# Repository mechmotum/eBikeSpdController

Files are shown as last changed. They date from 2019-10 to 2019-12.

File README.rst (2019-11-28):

eBikeSpdController
==================

This repo contains the source files for the design, implementation and testing of a cruise control system for an instrumented electric bicycle. Additionally, this repo contains project documentation in the form of a user/technical guide and master electrical schematic for the cruise control system. Newcomers to this project should begin by reading the user/technical guide.  

Controller Design Source Code
-----------------------------
The design folder contains MATLAB code that can be used to replicate the results of the controller design process outlined in this blog post here: https://mechmotum.github.io/blog/ebike-controller-design.html 

To replicate the controller design process, download the .m files in the design folder and run them in 
the following order: SystemID.m -> ControllerTuning.m -> ControllerRobustnessTesting.m -> ControllerEval.m. 
For more information, see the blog post mentioned above.

Implementation Source Code 
--------------------------
The Implementation folder contains the .ino file used to implement the derived contoller on an Arduino nano augmented to the powertrain of an electric bicycle. Please see this blog post for more information on how this software fits into the overall system: 
https://mechmotum.github.io/blog/ebike-controller-implementation.html

Testing Source Code 
-------------------
The Testing folder contains the source code used in the evaluation and diagnostics of the cruise control system implementation. The boxplot figure codes contain the code used to create the boxplot figures shown in the paper and poster presented at the 2019 Bicycle and Motorcycle Dynamics Conference. These materials can be found here: https://mechmotum.github.io/blog/ebike-controller-bmd-presentation.html 

Also included in the Testing folder is a utility function for converting bits to volts and the testAnalyzer.m file used to plot and evaluate the performance of runs collected from testing. 

Please see each file for more information on what's included in them. These files are meant to be used with the comma delimited diagnostics files produced by the TopLevel.ino file found in the Implementation folder of this repo. 

Other Documents in this Repo
---------------------------- 
Also included in this repository are the user+technical guide for the cruise control system (pdf) and a copy of the master electrical schematic for the cruise control system (pdf). Note: The master electrical schematic is also included as a .json file for opening and editing in easyEDA.

Prerequisites
-------------

Software

You will need MATLAB R2018b or above with the Control System and Robust Control Toolboxes installed. Also needed is the Arduino IDE with the 
PID_v1 and PinChangeInterrupt libraries. 

Hardware 

Hardware prerequisites can be found on the implementation blog post mentioned above.

Authors
-------

Trevor Metz 
UC Davis Mechanical Engineering 2019
tzmetz@ucdavis.edu

Acknowledgments
---------------
Jason K. Moore for support and guidance 

Nicholas Chan for help with the Arduino code 

Brett Beauregard for developing the PID Arduino Library heavily used in the Implementation code 

Grey Gnome for developing the pin change interrupt library used in the Implementation code

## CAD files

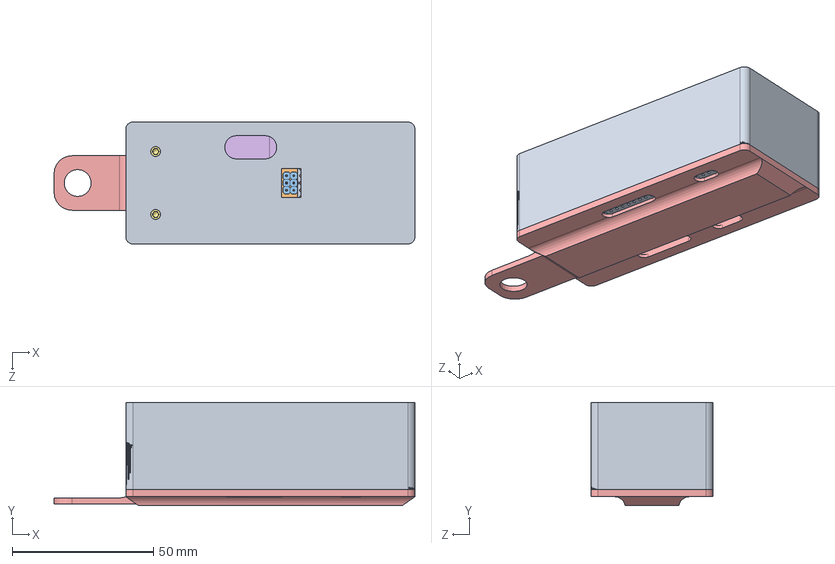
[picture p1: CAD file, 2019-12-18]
CADfiles/Nano Housing/Arduino Housing Master Assembly.SLDASM
127.8 x 36.5 x 43.2 mm
Arduino Nano V3 PCB.ipt
Housing male header - single.ipt x 36
Pin male header straight - single.ipt x 36
Base_ArduinoHousing
socket head cap screw_am x 2
HeatSetInsert x 2
FlatTopNanoHousingCover

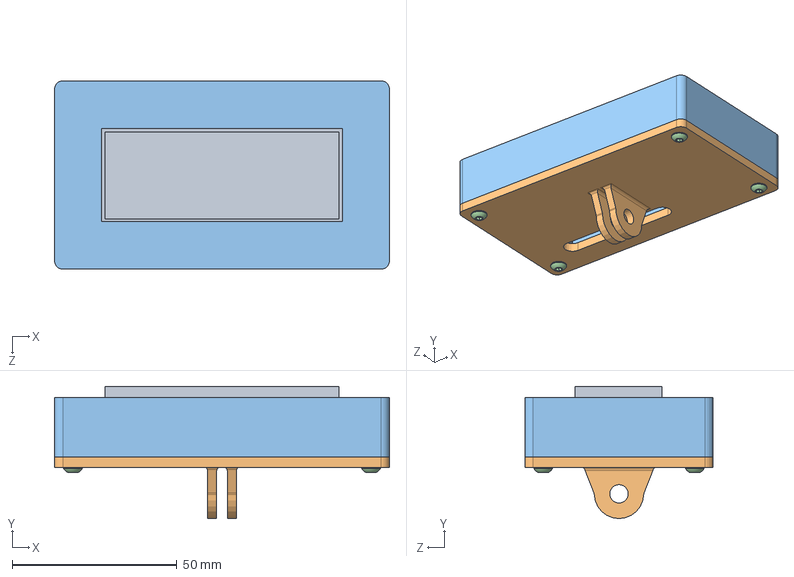
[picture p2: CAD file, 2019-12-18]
CADfiles/LCD Housing/LCDHousing_Assem_G2.SLDASM
101.6 x 40.1 x 57.1 mm
LCD_G2
LCDHousing_Bot_G2
LCDHousing_Top_G2
socket button head cap screw_am x 4
HeatSetInsert x 4

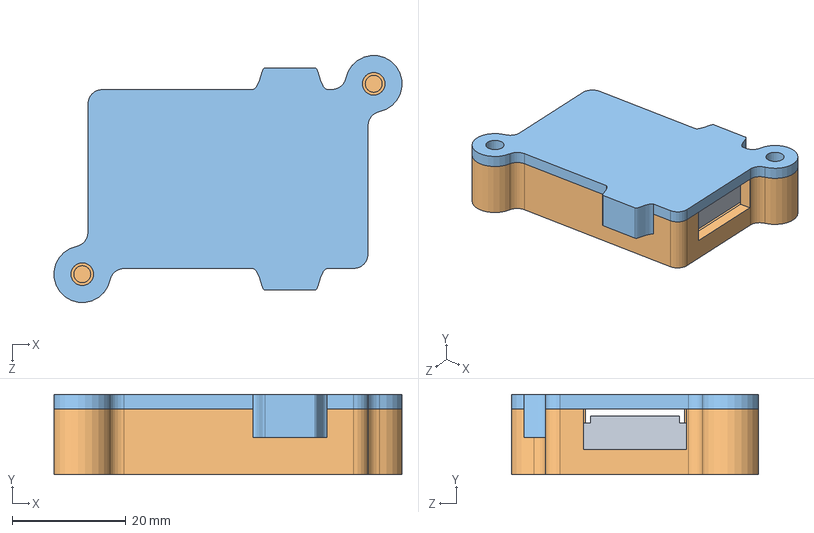
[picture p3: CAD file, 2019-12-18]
CADfiles/MicroSDCardHousing/M_SDCardHousing_MasterAssem.SLDASM
61.3 x 14.1 x 43.5 mm
microSDCardModule
Base_MicroSDCardModule
cover_MSDHousing

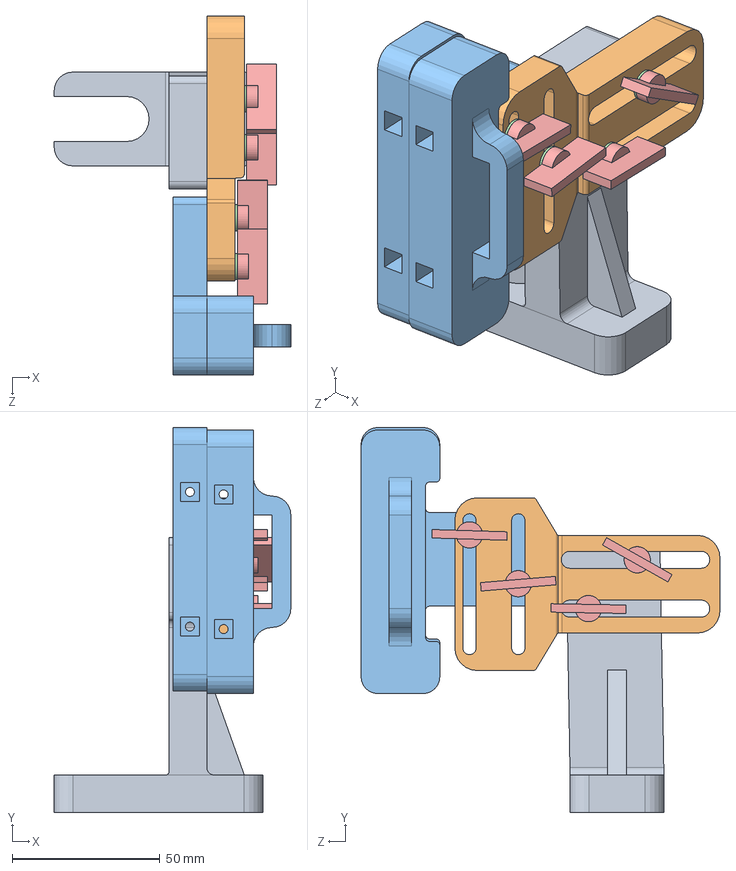
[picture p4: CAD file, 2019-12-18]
CADfiles/SafetySwitch/ReedSwitch/ReedSwitchAssemV2.SLDASM
80.1 x 130.3 x 121.4 mm
StayClamp_Top
AdjusterArm
SwitchMountBot x 2
M4Washer x 8
WingNut x 4

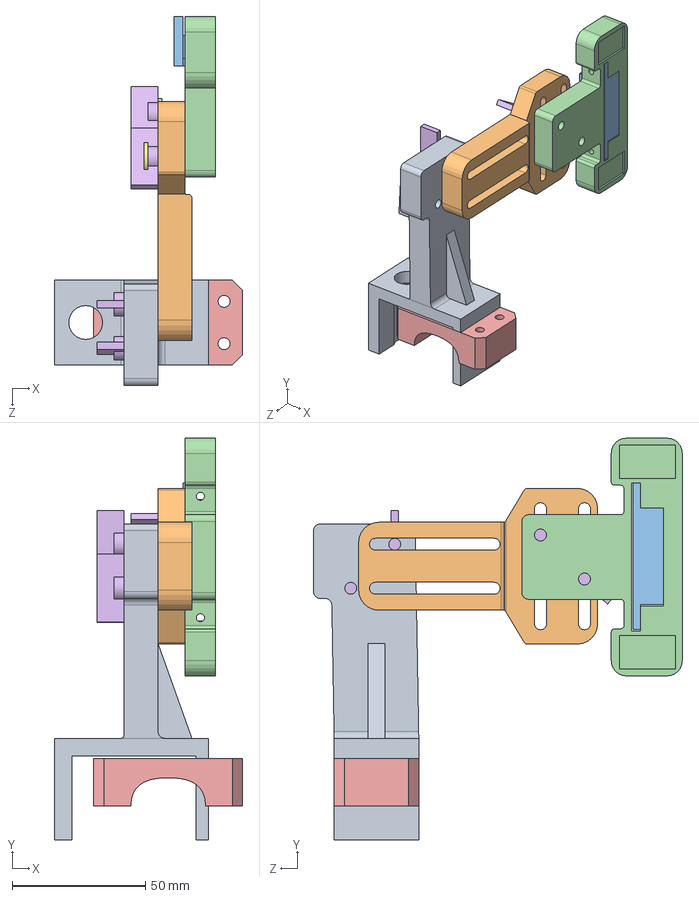
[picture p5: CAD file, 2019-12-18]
CADfiles/SafetySwitch/ReedSwitch/ReedSwitchAssem.SLDASM
70.7 x 150.7 x 138.4 mm
StayClamp_Top
AdjusterArm
ReedSwitchBlank
SwitchMountBot
StayClamp_Bot
WingNut x 4
flat washer regular_am x 4

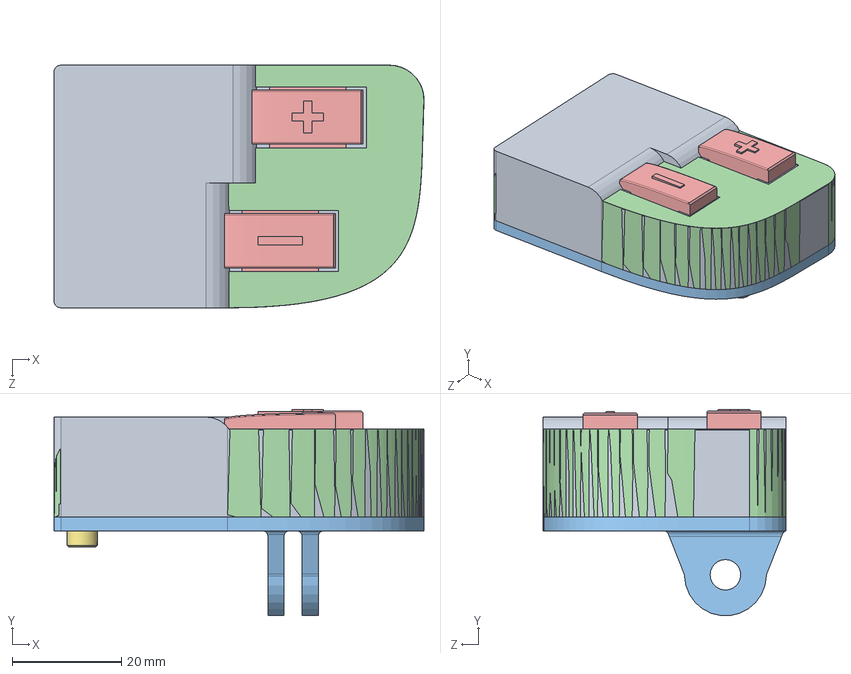
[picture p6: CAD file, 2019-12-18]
CADfiles/Button Housing/MasterAssembly.SLDASM
67.7 x 37.7 x 44.5 mm
PerfBoard
PushButton x 2
ButHousing_Base
ButtHousingCoverV2

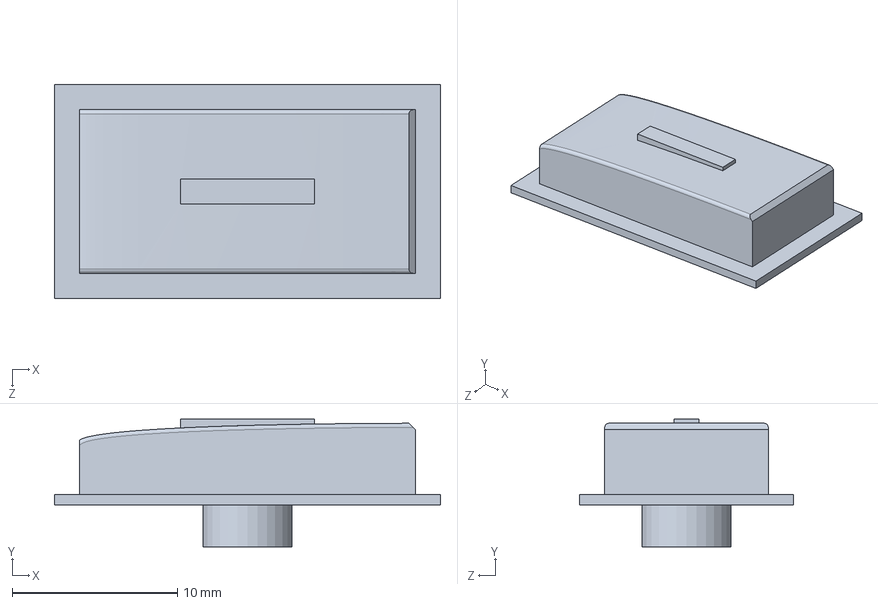
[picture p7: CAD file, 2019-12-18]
CADfiles/Button Housing/Button.SLDPRT
23.4 x 7.75 x 13.0 mm

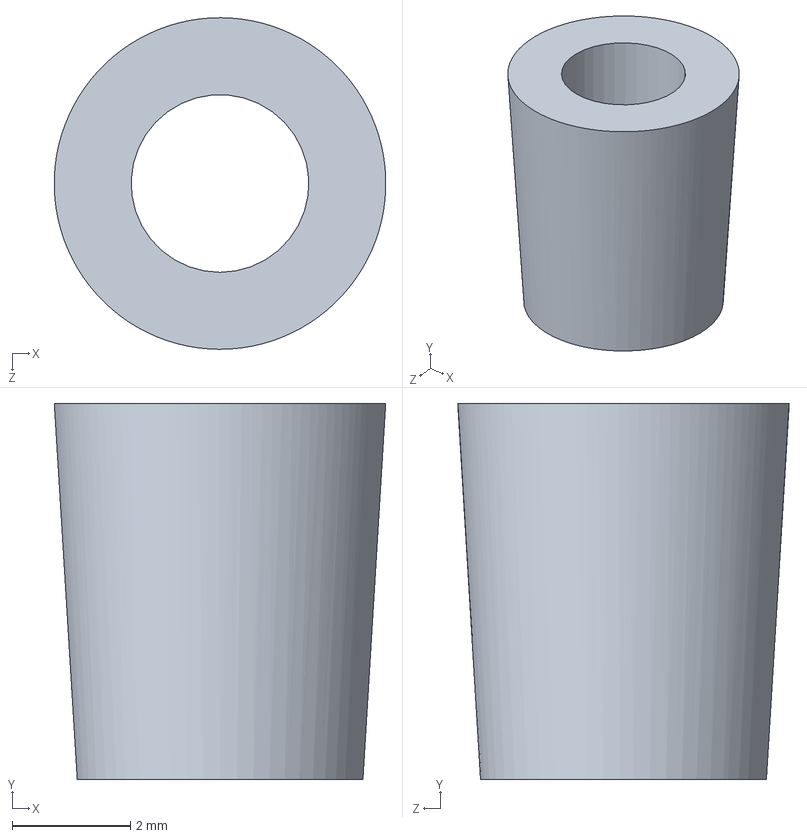
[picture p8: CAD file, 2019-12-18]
CADfiles/HeatSetInsert.SLDPRT
5.60 x 6.35 x 5.60 mm

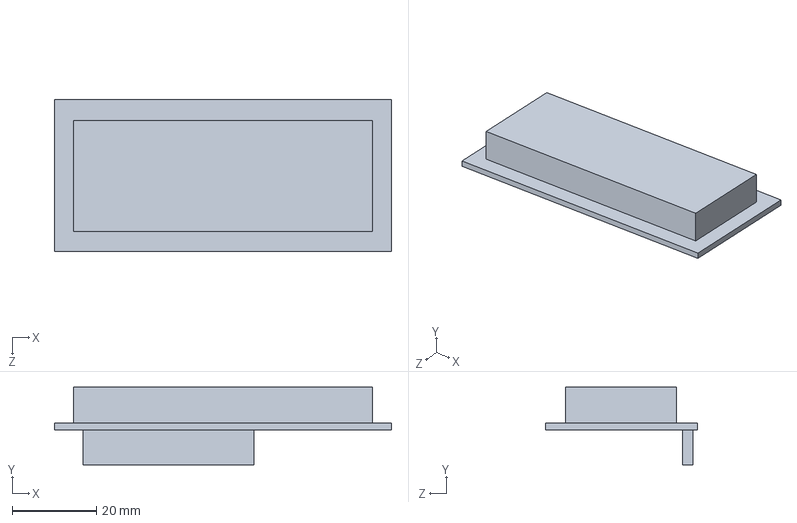
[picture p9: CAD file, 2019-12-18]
CADfiles/LCD Housing/LCD_G2.SLDPRT
79.9 x 18.5 x 36.0 mm

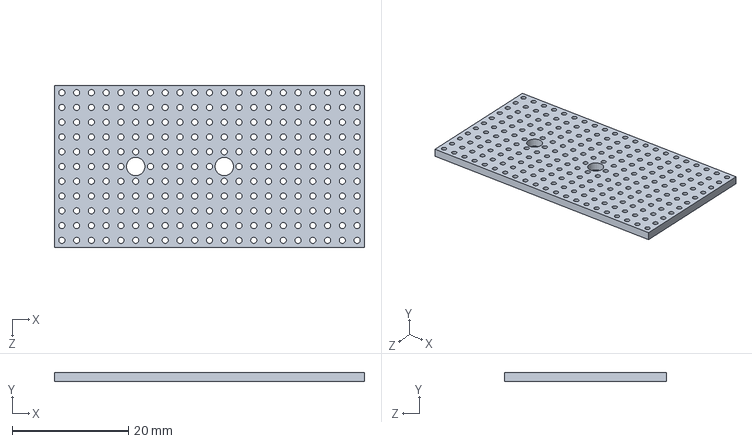
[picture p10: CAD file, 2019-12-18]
CADfiles/Nano Housing/StripBoard.SLDPRT
53.3 x 1.59 x 27.9 mm

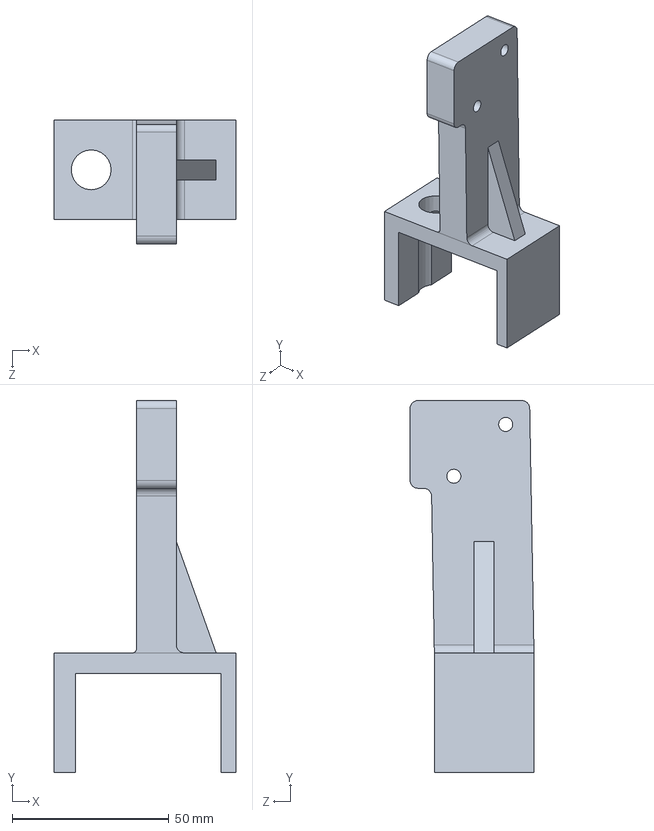
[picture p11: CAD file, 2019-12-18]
CADfiles/SafetySwitch/ReedSwitch/StayClamp_Top.SLDPRT
57.9 x 118.5 x 39.5 mm

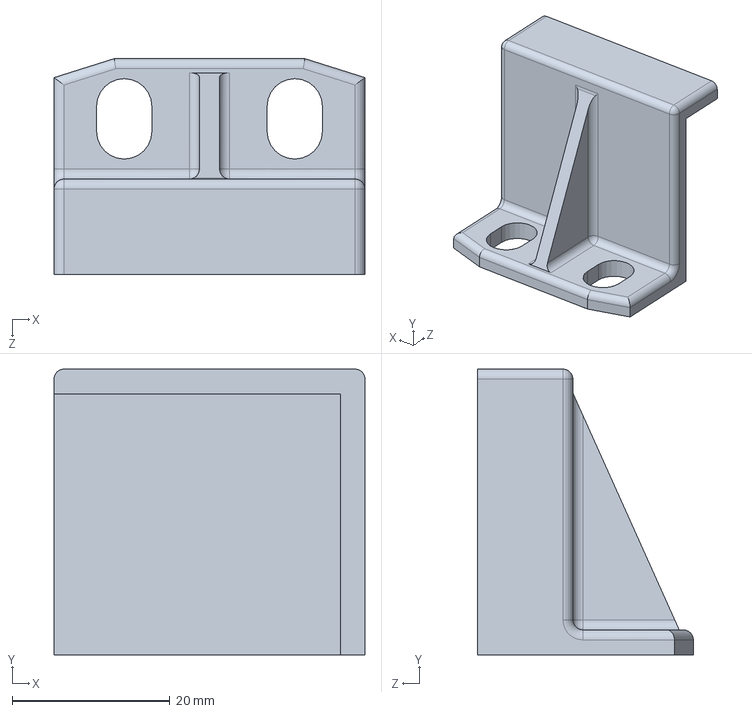
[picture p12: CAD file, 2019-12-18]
CADfiles/SafetySwitch/Relay Clamp Top.SLDPRT
39.4 x 36.2 x 27.3 mm

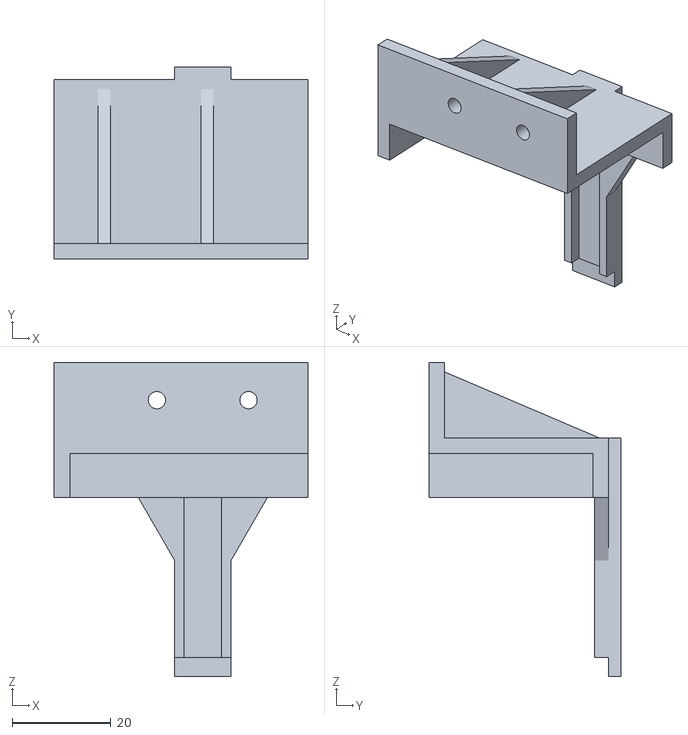
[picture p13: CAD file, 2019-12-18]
CADfiles/SafetySwitch/STL/Relay Clamp Bot_NOFILLET.STL
51.3 x 38.9 x 63.5

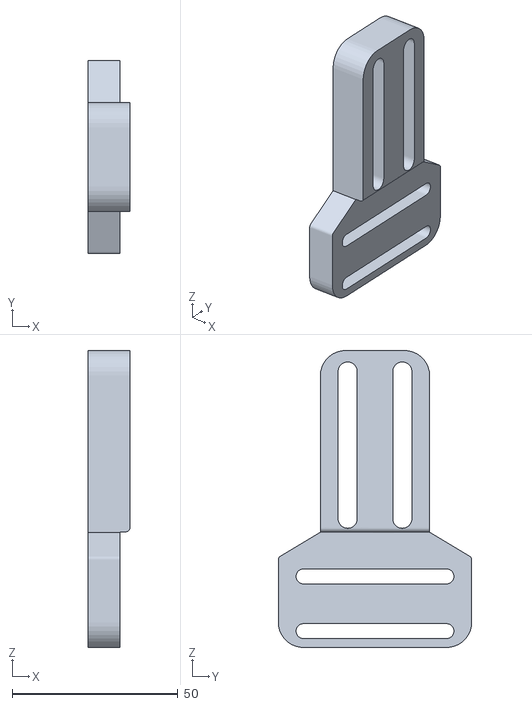
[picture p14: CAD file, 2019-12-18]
CADfiles/SafetySwitch/STL/V2 Reed Switch/AdjusterArm.STL
12.7 x 58.4 x 89.7

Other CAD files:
CADfiles/Nano Housing/Arduino Nano V3 assemble.SLDASM
CADfiles/MicroSDCardHousing/Base_MicroSDCardModule.sldprt
CADfiles/Button Housing/ButtHousingCoverV2.sldprt
CADfiles/LCD Housing/LCDHousing_Top_G2.sldprt
CADfiles/Button Housing/ButHousing_Base.sldprt
CADfiles/Button Housing/ButHousing_Top.sldprt
CADfiles/Button Housing/PerfBoard.SLDPRT
CADfiles/Button Housing/PushButton.SLDPRT
CADfiles/Button Housing/Spring.SLDPRT
CADfiles/LCD Housing/LCDHousing_Bot_G2.SLDPRT
CADfiles/MicroSDCardHousing/cover_MSDHousing.sldprt
CADfiles/MicroSDCardHousing/microSDCardModule.SLDPRT
CADfiles/Nano Housing/Base_ArduinoHousing.sldprt
CADfiles/Nano Housing/Cover_ArduinoHousing.sldprt
CADfiles/Nano Housing/FlatTopNanoHousingCover.sldprt
CADfiles/Nano Housing/arduino-nano-v3/Arduino Nano V3 PCB.ipt
CADfiles/Nano Housing/arduino-nano-v3/Arduino Nano V3 assemble.iam
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

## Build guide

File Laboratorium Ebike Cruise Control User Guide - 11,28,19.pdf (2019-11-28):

## Laboratorium Electric Bicycle Cruise Control System Operating and Technical Guide

Introduction
This guide is here to help you understand both how to use the cruise control system and how to understand the technical details behind the design and implementation of the cruise control system.

Cruise Control System User’s Guide
The cruise control system maintains the electric bicycle’s speed at a user set desired speed in m/s. This action is performed through automatic modulation of the throttle via an Arduino nano programmed with a simple PID controller. The Arduino Nano sits inline with the throttle output signal. When the cruise control is engaged, the Ardino works by emulating the rider’s throttle inputs to maintain the speed of the electric bicycle at the user set desired speed.

The cruise control system can be engaged when riding the bike. The following outlines the steps the user needs to take to engage and operate the cruise control:

1. To power all systems the following needs to be performed:
a. Before beginning, make sure that the dead man’s ankle velcro switch is attached to its mount near the foot peg
b. First power the Arduino nano and dead man’s switch by flipping the switch to the NiCd battery pack. The onboard Arduino LEDs will flicker on.
c. Next power the electric bicycle by flipping the rocker switch on the bottom of the Li+ battery cylinder on the seat tube. To verify the battery switch is in the “on” position, press the battery level indicator button on the top of the battery. There should be an array of multicolored LEDs that light up showing the current capacity of the battery.
d. Finally, press the red switch on the side of the throttle. The LEDs on the throttle will light up indicating the bicycle is ready for riding
2. With the dead man’s ankle velcro switch still attached to the bicycle, tie the switch to the rider’s ankle. Another person may be needed to hold the bicycle upright.
3. Start riding the bicycle.
4. Accelerate or deccelerate to around the desired setpoint (target) speed.

5. Engage the cruise control by pressing the two cruise control buttons at the same time. The LCD screen will change to show the setpoint speed and the current speed.
a. Note that the setpoint speed initializes itself at the speed of the bicycle the moment the cruise control is engaged.
6. Once engaged, the Arduino Nano will take control of the throttle and the user can sit back and steer.
a. At any time, manual control of the throttle can be returned to the user by simply pressing all the way down on the throttle with your thumb (This will deactivate the cruise control).
7. While the cruise control is engaged the cruise control buttons can be pressed to either increment or decrement the setpoint speed.
8. To disengage the cruise control simply press all the way down on the throttle. A message confirming that the cruise control has disengaged will print to the LCD.
9. Steps 4-8 can be repeated any time during the ride

Reverting the Electric Bicycle to its Original Powertrain
To revert the electric bicycle back to its original powertrain, the throttle output signal (from its hall effect sensor) needs to be jumped directly to the motor controller. See below for the steps on how to do this.
1. Locate the throttle junction. This is located around the top triangle of the frame right above the head tube. See the picture below for reference:

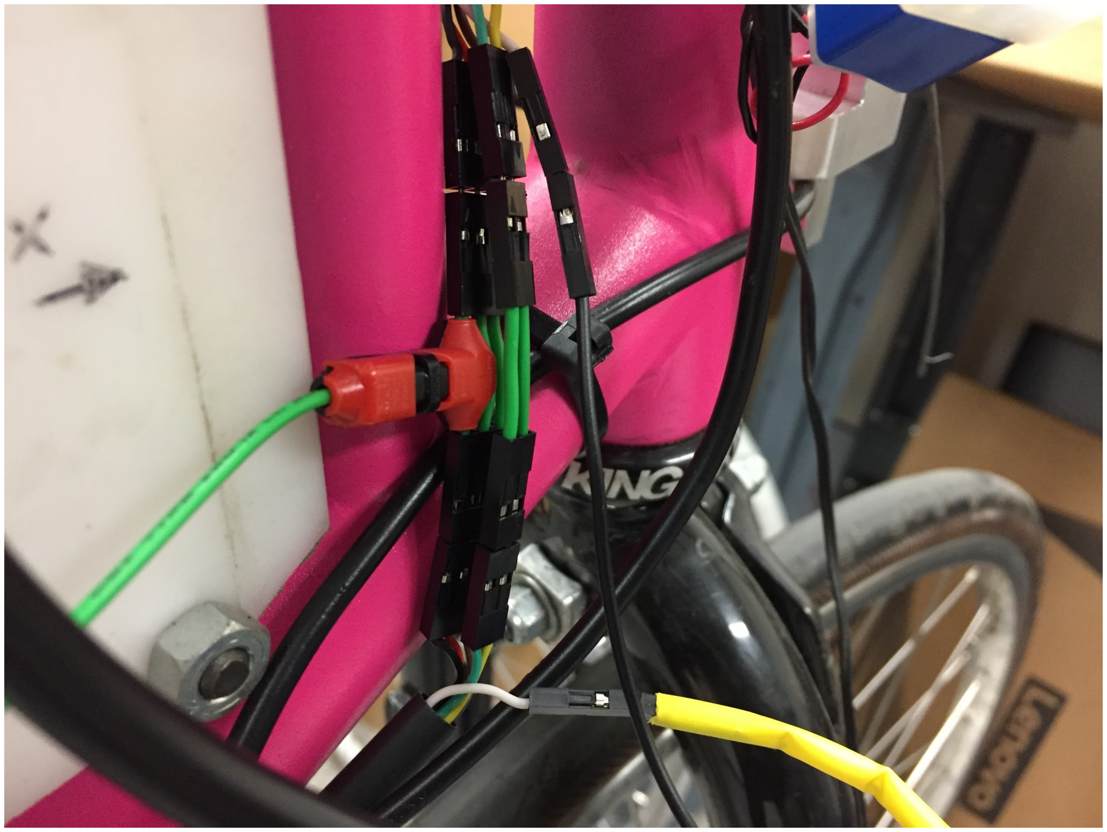
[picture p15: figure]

Note: The schematic for this junction can be found on sheet 3 of the master electrical schematic
2. Once located, disconnect the black and yellow wires. (Note the yellow wire is sleeved in a yellow sleeve).
3. To jump the throttle signal directly to the motor controller you will need to add a jumper wire to connect the white wires together. The picture below shows the jumper wire used to connect both the white wires together.

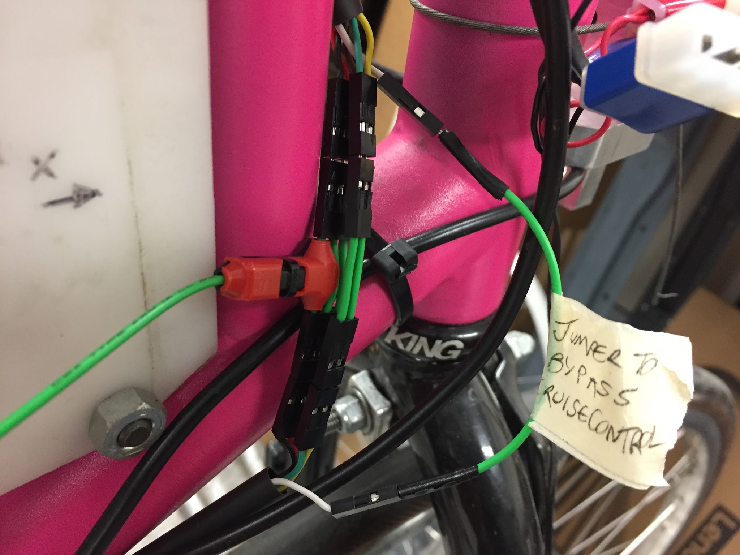
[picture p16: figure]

4. Once this is complete the Arduino should have no effect on the bike’s powertrain and it should work normally again.

Cruise Control System Technical Guide
This technical guide is meant to help you understand what went into the design and implementation of the cruise control system. There is a number of documents regarding the technical details and design of the cruise control system; these are outlined here:
1. Project Technical Poster and Paper (https://mechmotum.github.io/blog/ebike-controller-bmd-presentation.html)
a. These give a good high level overview of the project and its technical details making them a good place to start
2. Davis Instrumented Bike (https://moorepants.github.io/dissertation/davisbicycle.html) (Wheel Rate and Calibration Sections)
a. This gives a good description of the instrumented bike platform and how to go about interacting with it
3. Controller Design Blog Post (https://mechmotum.github.io/blog/ebike-controller-design.html)
a. This blog post outlines the details of the controller design process used to derive and tune the PID controller
4. Project Code Description (See eBikeSpdController Github Repository Read Me)
a. This Read Me outlines the files contained in the repository
5. Controller Design MATLAB Code (https://github.com/mechmotum/eBikeSpdController/tree/master/Design)

6. Controller Implementation Blog Post (https://mechmotum.github.io/blog/ebike-controller-implementation.html)
a. This blog post describes the physical implementation of the PID controller onto the electric bicycle
7. Arduino Code (https://github.com/mechmotum/eBikeSpdController/tree/master/Implementation/TopLevel)
8. System Electrical Schematic (https://github.com/mechmotum/eBikeSpdController)

Reading these documents in the order suggested here should give you a good enough understanding of the technical design and details of the cruise control system in order to make modifications or adjustments to the system.

Technical Troubleshooting Tips
Over the course of working on the bike, a couple common issues have arisen. These are detailed below:
1. Anderson Power Pole Contacts
a. Issue: Arduino won't power on or dead man’s switch is malfunctioning
b. Fix: Adnerson power poles either on the 14 AWG wire from the Li+ battery or the 22 AWG wire from the NiCd battery have loose contacts.
i. These contacts will need to be manually pressed back into place by pressing on them from the back of the housing with a small diameter screwdriver or Allen wrench
1. It helps to do this while the two connectors are connected to each other. CAUTION: DO NOT SHORT THE BATTERY
ii. | It’s a good idea to check that these contacts are fully in place every
| time the connectors are connected/disconnected as they come
| loose easily
1. To do this look at the rear of the connector housing and see if
| the contact is sticking out further than typical
2. NiCd Battery Charge
a. Issue: Arduino won't power on or dead man’s switch is malfunctioning
b. Fix: Charge the NiCd batteries via the 14.2V terminal
i. NOTE: I don’t believe there is any over/under charge protection built
| into the batteries and don’t trust the charger so it is important to
| periodically check the battery voltage and temperature while
| charging these batteries
ii. | The same goes with discharging the batteries. They should be
| periodically checked to ensure they are not overdischarged while
| being used to power the Arduino

iii. Read up on charging NiCd Batteries https://batteryuniversity.com/learn/article/charging_nickel_based_ba tteries (https://batteryuniversity.com/learn/article/charging_nickel_based_batteries)

3. Dupont Connectors
a. Issue: there is an open circuit somewhere
b. Fix: Check the Dupont connectors. Typically the 1x1 Dupont connectors have been found to come loose. There is a 1x1 Dupont connector on the dead man’s switch circuit that has come loose before (it is currently wrapped in heat shrink tubing)

### 4. Arduino Board Solder Joints

a. Issue: Open Circuit
b. Fix: Check the solder joints on the Arduino board as, over time, these may break
5. Battery Low Voltage Imbalance
a. Issue: Bike motor cuts out after a few seconds of riding
b. Fix: Check the Li+ battery. If the cells in the battery become out of balance they will trigger the low voltage cut off of the battery management system in the Li+ battery and cut power to the bike. To check this you will need to disassemble the Li+ battery and probe the voltage of each cell on the battery management board. If you find a significant imbalance between cells this will justify buying a new battery
6. Motor not spinning up
a. Issue: Motor won’t spin up even though everything else is working/seems right
b. Fix: Check the brake levers. Sometimes the metal bracket that contacts the brake lever safety switch will get stuck outside the brake lever housing. Reinsert this metal bracket to fix the brake lever safety switch and get the motor to start up again.

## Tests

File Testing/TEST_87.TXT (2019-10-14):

0,0.00,170,0.04,2.86,0.00,9.48,0,0,0,0,0,3.00
0,0.00,170,0.04,2.96,0.00,9.57,0,0,0,0,0,4.00
0,0.00,170,0.04,3.02,0.00,9.61,0,0,0,0,0,2.00
0,0.00,170,0.04,3.11,0.00,9.65,0,0,0,0,0,8.00
0,0.00,170,0.04,3.33,0.00,9.69,0,0,0,0,0,5.00
0,0.00,170,0.05,3.56,0.00,9.74,0,0,0,0,0,2.00
0,0.00,170,0.05,3.68,0.00,9.78,0,0,0,0,0,2.00
0,0.00,169,0.05,3.68,0.00,9.82,0,0,0,0,0,2.00
0,0.00,170,0.05,3.57,0.00,9.86,0,0,0,0,0,1.00
0,0.00,170,0.04,3.38,0.00,9.90,0,0,0,0,0,1.00
0,0.00,170,0.04,3.11,0.00,9.94,0,0,0,0,0,1.00
0,0.00,170,0.03,2.78,0.00,9.98,0,0,0,0,0,0.00
0,0.00,169,0.03,2.45,0.00,10.02,0,0,0,0,0,1.00
0,0.00,170,0.03,2.14,0.00,10.06,0,0,0,0,0,2.00
0,0.00,170,0.02,1.87,0.00,10.10,0,0,0,0,0,0.00
0,0.00,170,0.02,1.62,0.00,10.14,0,0,0,0,0,1.00
0,0.00,170,0.02,1.39,0.00,10.18,0,0,0,0,0,0.00
0,0.00,170,0.01,1.17,0.00,10.22,0,0,0,0,0,1.00
0,0.00,170,0.01,1.00,0.00,10.27,0,0,0,0,0,1.00
0,0.00,170,0.01,0.93,0.00,10.31,0,0,0,0,0,5.00
0,0.00,170,0.01,1.05,0.00,10.35,0,0,0,0,0,5.00
0,0.00,170,0.01,1.29,0.00,10.39,0,0,0,0,0,1.00
0,0.00,170,0.02,1.55,0.00,10.43,0,0,0,0,0,4.00
0,0.00,170,0.02,1.80,0.00,10.47,0,0,0,0,0,3.00
0,0.00,170,0.02,2.03,0.00,10.51,0,0,0,0,0,2.00
0,0.00,170,0.03,2.25,0.00,10.55,0,0,0,0,0,6.00
0,0.00,170,0.03,2.54,0.00,10.59,0,0,0,0,0,4.00
0,0.00,170,0.03,2.81,0.00,10.63,0,0,0,0,0,1.00
0,0.00,170,0.04,2.95,0.00,10.67,0,0,0,0,0,2.00
0,0.00,170,0.04,2.99,0.00,10.71,0,0,0,0,0,2.00
0,0.00,170,0.04,2.95,0.00,10.75,0,0,0,0,0,1.00
0,0.00,170,0.04,2.84,0.00,10.79,0,0,0,0,0,2.00
0,0.00,170,0.03,2.70,0.00,10.83,0,0,0,0,0,1.00
0,0.00,170,0.03,2.52,0.00,10.88,0,0,0,0,0,2.00
0,0.00,170,0.03,2.37,0.00,10.92,0,0,0,0,0,2.00
0,0.00,170,0.03,2.26,0.00,10.95,0,0,0,0,0,3.00
0,0.00,170,0.03,2.20,0.00,11.00,0,0,0,0,0,3.00
0,0.00,170,0.03,2.19,0.00,11.04,0,0,0,0,0,2.00
0,0.00,170,0.03,2.17,0.00,11.08,0,0,0,0,0,1.00
0,0.00,170,0.03,2.10,0.00,11.12,0,0,0,0,0,1.00
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

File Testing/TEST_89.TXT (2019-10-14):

0,0.00,169,0.01,0.95,0.00,9.48,0,0,0,0,0,1.00
0,0.00,169,0.01,0.92,0.00,9.57,0,0,0,0,0,0.00
0,0.00,169,0.01,0.92,0.00,9.61,0,0,0,0,0,5.00
0,0.00,169,0.01,1.17,0.00,9.65,0,0,0,0,0,11.00
0,0.00,169,0.02,1.65,0.00,9.69,0,0,0,0,0,1.00
0,0.00,169,0.02,2.08,0.00,9.74,0,0,0,0,0,1.00
0,0.00,169,0.03,2.33,0.00,9.78,0,0,0,0,0,1.00
0,0.00,169,0.03,2.44,0.00,9.82,0,0,0,0,0,1.00
0,0.00,169,0.03,2.47,0.00,9.86,0,0,0,0,0,4.00
0,0.00,169,0.03,2.49,0.00,9.90,0,0,0,0,0,0.00
0,0.00,169,0.03,2.42,0.00,9.94,0,0,0,0,0,0.00
0,0.00,169,0.03,2.23,0.00,9.98,0,0,0,0,0,0.00
0,0.00,170,0.02,1.99,0.00,10.02,0,0,0,0,0,0.00
0,0.00,169,0.02,1.72,0.00,10.06,0,0,0,0,0,0.00
0,0.00,170,0.02,1.43,0.00,10.10,0,0,0,0,0,0.00
0,0.00,169,0.01,1.16,0.00,10.14,0,0,0,0,0,0.00
0,0.00,169,0.01,0.90,0.00,10.18,0,0,0,0,0,0.00
0,0.00,169,0.01,0.69,0.00,10.22,0,0,0,0,0,1.00
0,0.00,169,0.00,0.54,0.00,10.27,0,0,0,0,0,1.00
0,0.00,170,0.00,0.47,0.00,10.31,0,0,0,0,0,2.00
0,0.00,169,0.00,0.47,0.00,10.35,0,0,0,0,0,0.00
0,0.00,169,0.00,0.48,0.00,10.39,0,0,0,0,0,1.00
0,0.00,169,0.00,0.50,0.00,10.43,0,0,0,0,0,0.00
0,0.00,169,0.00,0.50,0.00,10.47,0,0,0,0,0,1.00
0,0.00,181,0.00,0.51,0.00,10.51,0,0,0,0,0,0.00
0,0.00,169,0.00,0.55,0.00,10.55,0,0,0,0,0,4.00
0,0.00,169,0.01,0.72,0.00,10.59,0,0,0,0,0,5.00
0,0.00,169,0.01,1.07,0.00,10.63,0,0,0,0,0,5.00
0,0.00,169,0.02,1.45,0.00,10.67,0,0,0,0,0,0.00
0,0.00,169,0.02,1.73,0.00,10.71,0,0,0,0,0,2.00
0,0.00,169,0.02,1.89,0.00,10.75,0,0,0,0,0,0.00
0,0.00,169,0.02,1.93,0.00,10.79,0,0,0,0,0,0.00
0,0.00,169,0.02,1.86,0.00,10.83,0,0,0,0,0,0.00
0,0.00,170,0.02,1.69,0.00,10.88,0,0,0,0,0,0.00
0,0.00,169,0.02,1.51,0.00,10.92,0,0,0,0,0,1.00
0,0.00,169,0.01,1.33,0.00,10.96,0,0,0,0,0,0.00
0,0.00,169,0.01,1.15,0.00,10.99,0,0,0,0,0,0.00
0,0.00,169,0.01,0.96,0.00,11.03,0,0,0,0,0,0.00
0,0.00,169,0.01,0.77,0.00,11.08,0,0,0,0,0,0.00
0,0.00,169,0.00,0.60,0.00,11.12,0,0,0,0,0,0.00
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

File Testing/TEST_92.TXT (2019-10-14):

0,0.00,170,0.08,5.72,0.00,9.49,0,0,0,0,0,6.00
0,0.00,170,0.08,5.89,0.00,9.58,0,0,0,0,0,7.00
0,0.00,170,0.08,5.98,0.00,9.62,0,0,0,0,0,6.00
0,0.00,170,0.08,6.04,0.00,9.66,0,0,0,0,0,4.00
0,0.00,170,0.08,5.99,0.00,9.71,0,0,0,0,0,4.00
0,0.00,170,0.08,5.83,0.00,9.75,0,0,0,0,0,3.00
0,0.00,170,0.07,5.58,0.00,9.79,0,0,0,0,0,3.00
0,0.00,170,0.07,5.25,0.00,9.83,0,0,0,0,0,2.00
0,0.00,170,0.06,4.86,0.00,9.87,0,0,0,0,0,2.00
0,0.00,170,0.06,4.44,0.00,9.91,0,0,0,0,0,2.00
0,0.00,170,0.05,4.00,0.00,9.95,0,0,0,0,0,1.00
0,0.00,170,0.04,3.51,0.00,9.99,0,0,0,0,0,1.00
0,0.00,171,0.04,3.07,0.00,10.03,0,0,0,0,0,1.00
0,0.00,171,0.03,2.65,0.00,10.07,0,0,0,0,0,0.00
0,0.00,171,0.03,2.22,0.00,10.11,0,0,0,0,0,0.00
0,0.00,171,0.02,1.80,0.00,10.15,0,0,0,0,0,1.00
0,0.00,171,0.02,1.48,0.00,10.19,0,0,0,0,0,3.00
0,0.00,171,0.01,1.30,0.00,10.23,0,0,0,0,0,2.00
0,0.00,171,0.01,1.21,0.00,10.27,0,0,0,0,0,1.00
0,0.00,171,0.01,1.18,0.00,10.31,0,0,0,0,0,3.00
0,0.00,171,0.01,1.20,0.00,10.36,0,0,0,0,0,1.00
0,0.00,171,0.01,1.21,0.00,10.40,0,0,0,0,0,0.00
0,0.00,171,0.01,1.20,0.00,10.44,0,0,0,0,0,2.00
0,0.00,171,0.01,1.18,0.00,10.48,0,0,0,0,0,0.00
0,0.00,170,0.01,1.13,0.00,10.52,0,0,0,0,0,0.00
0,0.00,170,0.01,1.06,0.00,10.56,0,0,0,0,0,1.00
0,0.00,170,0.01,0.99,0.00,10.60,0,0,0,0,0,1.00
0,0.00,171,0.01,0.92,0.00,10.64,0,0,0,0,0,0.00
0,0.00,170,0.01,0.84,0.00,10.68,0,0,0,0,0,0.00
0,0.00,171,0.01,0.77,0.00,10.72,0,0,0,0,0,2.00
0,0.00,170,0.01,0.74,0.00,10.76,0,0,0,0,0,1.00
0,0.00,171,0.01,0.74,0.00,10.81,0,0,0,0,0,0.00
0,0.00,170,0.01,0.71,0.00,10.84,0,0,0,0,0,0.00
0,0.00,170,0.01,0.69,0.00,10.89,0,0,0,0,0,3.00
0,0.00,171,0.01,0.73,0.00,10.93,0,0,0,0,0,1.00
0,0.00,170,0.01,0.80,0.00,10.97,0,0,0,0,0,1.00
0,0.00,171,0.01,0.86,0.00,11.00,0,0,0,0,0,1.00
0,0.00,170,0.01,0.93,0.00,11.05,0,0,0,0,0,2.00
0,0.00,170,0.01,1.02,0.00,11.09,0,0,0,0,0,2.00
0,0.00,171,0.01,1.11,0.00,11.13,0,0,0,0,0,0.00
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

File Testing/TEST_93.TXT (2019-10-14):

0,0.00,169,0.01,0.95,0.00,9.18,0,0,0,0,0,1.00
0,0.00,169,0.01,0.97,0.00,9.28,0,0,0,0,0,1.00
0,0.00,169,0.01,0.96,0.00,9.32,0,0,0,0,0,0.00
0,0.00,169,0.01,0.94,0.00,9.36,0,0,0,0,0,1.00
0,0.00,169,0.01,0.91,0.00,9.40,0,0,0,0,0,1.00
0,0.00,169,0.01,0.89,0.00,9.44,0,0,0,0,0,1.00
0,0.00,169,0.01,0.87,0.00,9.48,0,0,0,0,0,0.00
0,0.00,169,0.01,0.84,0.00,9.52,0,0,0,0,0,1.00
0,0.00,169,0.01,0.81,0.00,9.56,0,0,0,0,0,1.00
0,0.00,169,0.01,0.80,0.00,9.60,0,0,0,0,0,1.00
0,0.00,169,0.01,0.79,0.00,9.65,0,0,0,0,0,0.00
0,0.00,169,0.01,0.75,0.00,9.69,0,0,0,0,0,0.00
0,0.00,169,0.01,0.69,0.00,9.73,0,0,0,0,0,0.00
0,0.00,169,0.00,0.61,0.00,9.77,0,0,0,0,0,0.00
0,0.00,169,0.00,0.52,0.00,9.81,0,0,0,0,0,0.00
0,0.00,169,0.00,0.43,0.00,9.85,0,0,0,0,0,0.00
0,0.00,169,0.00,0.34,0.00,9.89,0,0,0,0,0,0.00
0,0.00,169,-0.00,0.26,0.00,9.93,0,0,0,0,0,0.00
0,0.00,169,-0.00,0.19,0.00,9.97,0,0,0,0,0,0.00
0,0.00,169,-0.00,0.13,0.00,10.01,0,0,0,0,0,0.00
0,0.00,169,-0.00,0.10,0.00,10.05,0,0,0,0,0,1.00
0,0.00,169,-0.00,0.09,0.00,10.09,0,0,0,0,0,0.00
0,0.00,169,-0.00,0.10,0.00,10.14,0,0,0,0,0,0.00
0,0.00,169,-0.00,0.14,0.00,10.18,0,0,0,0,0,3.00
0,0.00,169,-0.00,0.27,0.00,10.22,0,0,0,0,0,3.00
0,0.00,169,0.00,0.49,0.00,10.26,0,0,0,0,0,2.00
0,0.00,169,0.01,0.71,0.00,10.30,0,0,0,0,0,0.00
0,0.00,169,0.01,0.85,0.00,10.33,0,0,0,0,0,0.00
0,0.00,169,0.01,0.92,0.00,10.38,0,0,0,0,0,1.00
0,0.00,169,0.01,0.99,0.00,10.42,0,0,0,0,0,3.00
0,0.00,169,0.01,1.11,0.00,10.46,0,0,0,0,0,2.00
0,0.00,169,0.01,1.27,0.00,10.50,0,0,0,0,0,3.00
0,0.00,170,0.02,1.45,0.00,10.54,0,0,0,0,0,2.00
0,0.00,173,0.02,1.64,0.00,10.58,0,0,0,0,0,3.00
0,0.00,315,0.02,1.82,0.00,10.62,0,0,0,0,0,3.00
0,0.00,419,0.02,2.00,0.00,10.66,0,0,0,0,0,3.00
0,0.00,442,0.03,2.20,0.00,10.70,0,0,0,0,0,4.00
0,0.00,457,0.03,2.41,0.00,10.74,0,0,0,0,0,3.00
0,0.00,460,0.03,2.61,0.00,10.78,0,0,0,0,0,3.00
0,0.00,460,0.03,2.78,0.00,10.82,0,0,0,0,0,4.00
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

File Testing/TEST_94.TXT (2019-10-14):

0,0.00,169,-0.00,0.00,0.00,9.18,0,0,0,0,0,0.00
0,0.00,169,-0.00,0.00,0.00,9.28,0,0,0,0,0,0.00
0,0.00,169,-0.00,0.00,0.00,9.32,0,0,0,0,0,0.00
0,0.00,169,-0.00,0.03,0.00,9.36,0,0,0,0,0,2.00
0,0.00,169,-0.00,0.12,0.00,9.41,0,0,0,0,0,1.00
0,0.00,169,-0.00,0.25,0.00,9.45,0,0,0,0,0,1.00
0,0.00,169,0.00,0.37,0.00,9.49,0,0,0,0,0,0.00
0,0.00,169,0.00,0.44,0.00,9.53,0,0,0,0,0,0.00
0,0.00,169,0.00,0.46,0.00,9.57,0,0,0,0,0,0.00
0,0.00,169,0.00,0.46,0.00,9.62,0,0,0,0,0,0.00
0,0.00,169,0.00,0.43,0.00,9.66,0,0,0,0,0,0.00
0,0.00,169,0.00,0.41,0.00,9.70,0,0,0,0,0,2.00
0,0.00,169,0.00,0.45,0.00,9.74,0,0,0,0,0,1.00
0,0.00,169,0.00,0.54,0.00,9.78,0,0,0,0,0,3.00
0,0.00,169,0.01,0.72,0.00,9.83,0,0,0,0,0,2.00
0,0.00,169,0.01,0.91,0.00,9.87,0,0,0,0,0,2.00
0,0.00,169,0.01,1.11,0.00,9.91,0,0,0,0,0,2.00
0,0.00,169,0.01,1.29,0.00,9.95,0,0,0,0,0,1.00
0,0.00,169,0.02,1.41,0.00,9.99,0,0,0,0,0,1.00
0,0.00,169,0.02,1.47,0.00,10.03,0,0,0,0,0,1.00
0,0.00,169,0.02,1.47,0.00,10.08,0,0,0,0,0,0.00
0,0.00,169,0.02,1.40,0.00,10.12,0,0,0,0,0,0.00
0,0.00,169,0.01,1.26,0.00,10.16,0,0,0,0,0,0.00
0,0.00,169,0.01,1.10,0.00,10.21,0,0,0,0,0,0.00
0,0.00,169,0.01,0.94,0.00,10.25,0,0,0,0,0,1.00
0,0.00,169,0.01,0.87,0.00,10.29,0,0,0,0,0,5.00
0,0.00,169,0.01,1.03,0.00,10.33,0,0,0,0,0,7.00
0,0.00,181,0.02,1.49,0.00,10.38,0,0,0,0,0,9.00
0,0.00,366,0.03,2.19,0.00,10.42,0,0,0,0,0,10.00
0,0.00,442,0.04,3.10,0.00,10.46,0,0,0,0,0,12.00
0,0.00,480,0.06,4.31,0.00,10.50,0,0,0,0,0,14.00
0,0.00,486,0.07,5.65,0.00,10.54,0,0,0,0,0,16.00
0,0.00,486,0.10,7.17,0.00,10.58,0,0,0,0,0,19.00
0,0.00,486,0.12,9.09,0.00,10.63,0,0,0,0,0,19.00
0,0.00,494,0.16,11.48,0.00,10.67,0,0,0,0,0,58.00
0,0.00,506,0.20,14.55,0.00,10.71,0,0,0,0,0,22.00
0,0.00,506,0.24,17.71,0.00,10.76,0,0,0,0,0,27.00
0,0.00,510,0.31,22.36,0.00,10.83,0,0,0,0,0,29.00
0,0.00,512,0.34,24.54,0.00,10.87,0,0,0,0,0,44.00
0,0.00,510,0.37,26.96,0.00,10.91,0,0,0,0,0,46.00
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

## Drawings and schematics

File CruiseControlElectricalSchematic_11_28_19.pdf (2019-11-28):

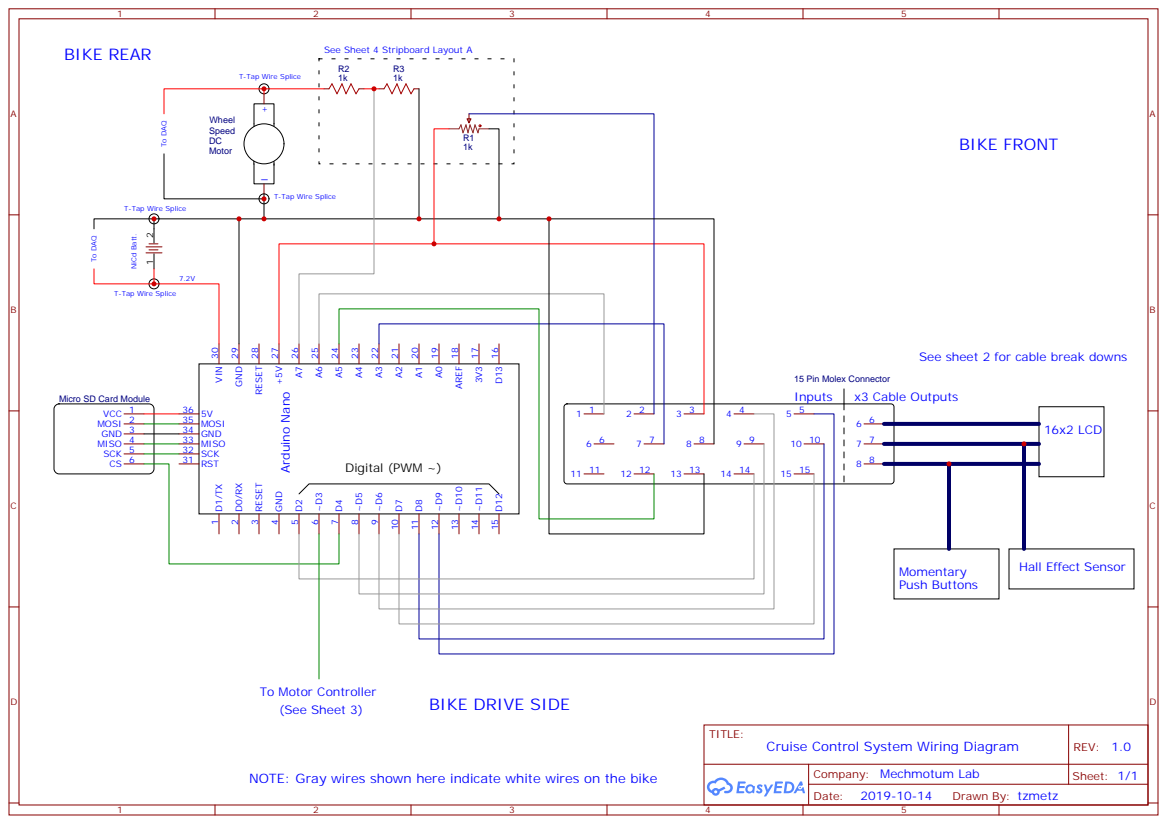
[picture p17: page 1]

T-Tap Wire Splice To DAQ

See sheet 2 for cable break downs

Micro SD Card Module

RST 31 SCK 32 MISO 33 GND 34 MOSI 35 5V 36

NOTE: Gray wires shown here indicate white wires on the bike

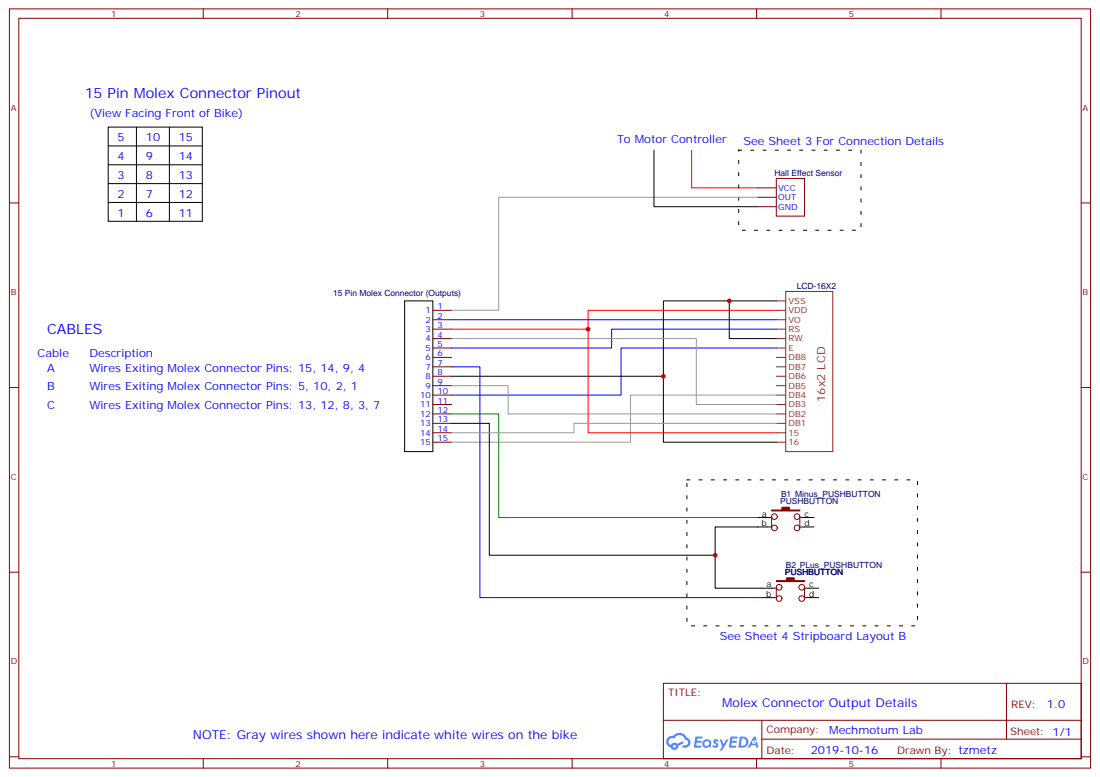
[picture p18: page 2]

15 Pin Molex Connector Pinout
(View Facing Front of Bike)

15 Pin Molex Connector (Outputs)

See Sheet 4 Stripboard Layout B

NOTE: Gray wires shown here indicate white wires on the bike

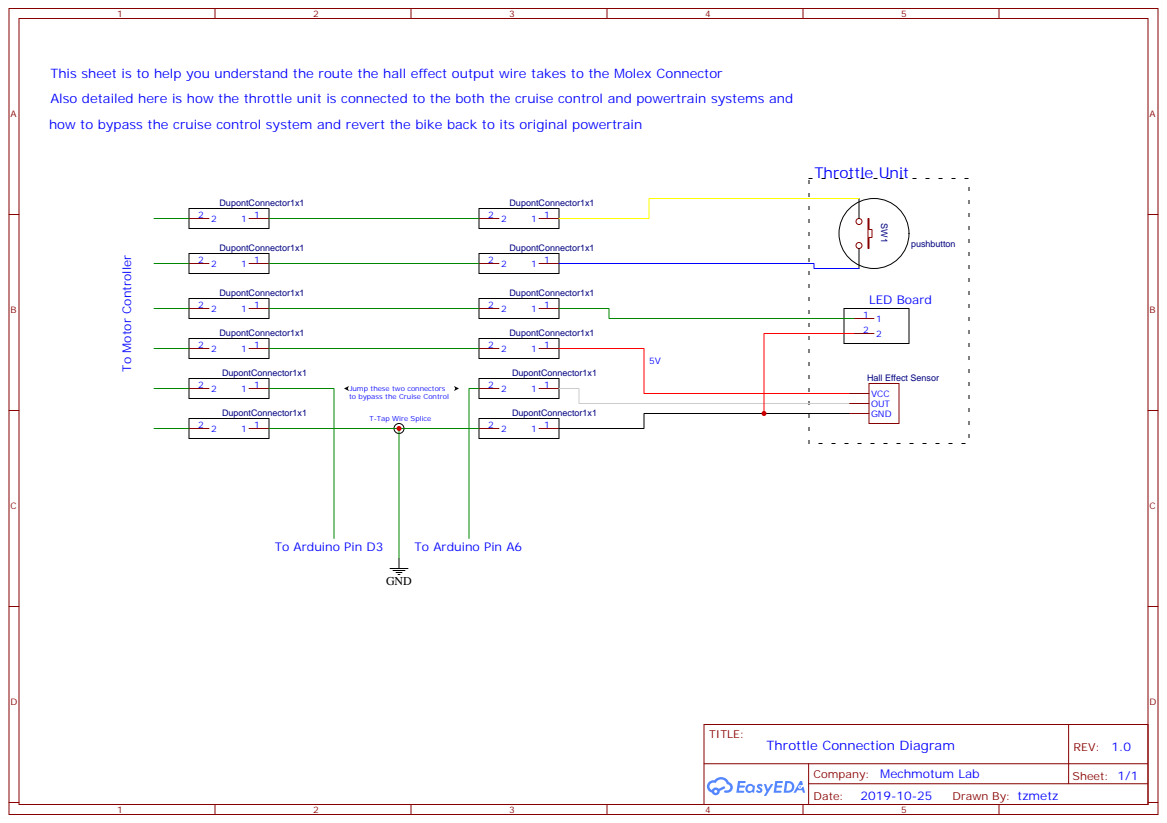
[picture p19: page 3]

This sheet is to help you understand the route the hall effect output wire takes to the Molex Connector
Also detailed here is how the throttle unit is connected to the both the cruise control and powertrain systems and
how to bypass the cruise control system and revert the bike back to its original powertrain

Jump these two connectors
to bypass the Cruise Control

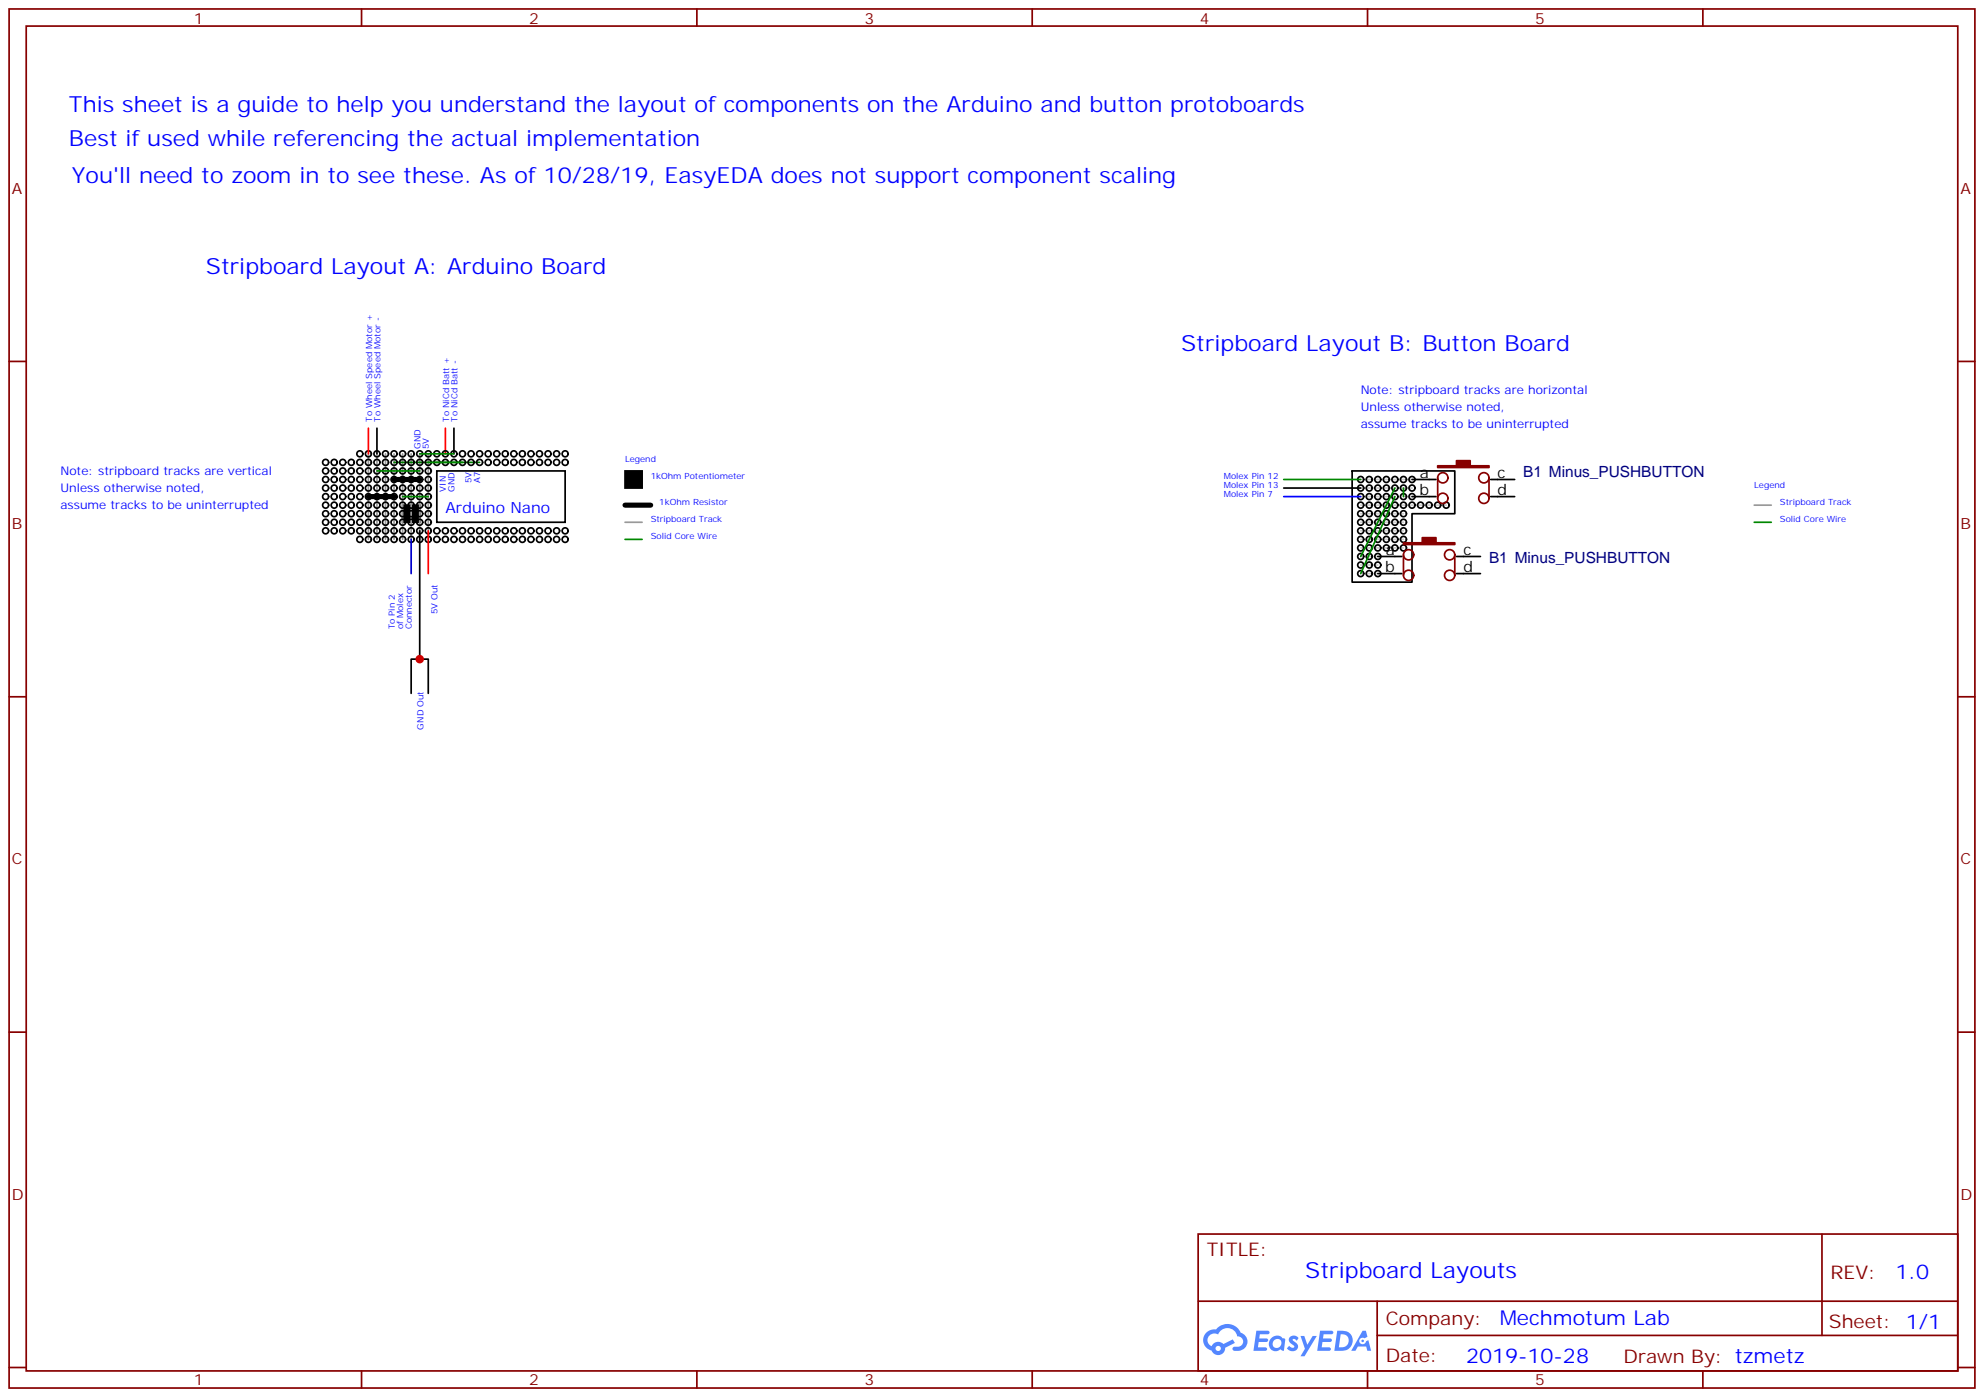
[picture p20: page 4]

This sheet is a guide to help you understand the layout of components on the Arduino and button protoboards
Best if used while referencing the actual implementation
You'll need to zoom in to see these. As of 10/28/19, EasyEDA does not support component scaling

Stripboard Layout A: Arduino Board

To Wheel Speed Motor +

To Wheel Speed Motor -

Stripboard Layout B: Button Board

VIN To NiCd Batt +

Note: stripboard tracks are horizontal
Unless otherwise noted,
assume tracks to be uninterrupted

Note: stripboard tracks are vertical

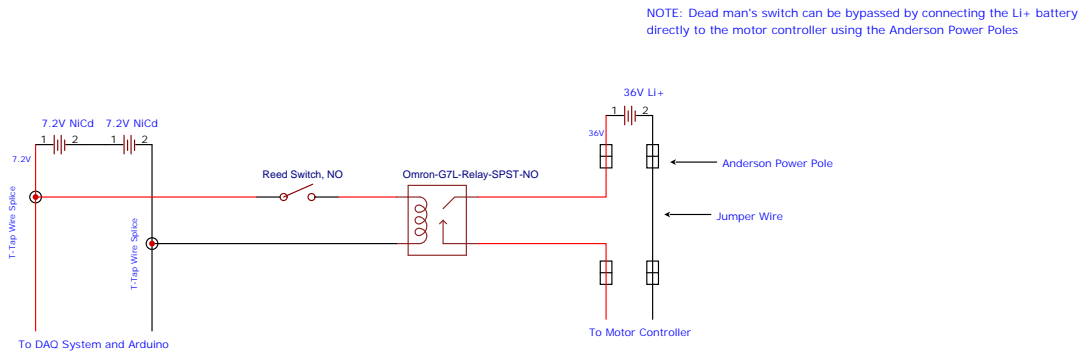
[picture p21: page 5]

NOTE: Dead man's switch can be bypassed by connecting the Li+ battery
directly to the motor controller using the Anderson Power Poles

To DAQ System and Arduino

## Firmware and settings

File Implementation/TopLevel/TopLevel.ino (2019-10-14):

/*               eBike Speed Controller Implementation Code             */               

/// DESCRIPTION 
///  This code implements a PID controller designed in MATLAB digitally on an Arduino nano 
///   to control the speed of an instrumented ebike. 

/// ACKNOWLEDGEMENTS
///  PID_v1 library can be downloaded from here: https://github.com/br3ttb/Arduino-PID-Library
///   PinChangeInterrupt Library can be downloaded from here: https://github.com/GreyGnome/PinChangeInt
///    Tutorial for PinChangeInterrupt Library can be found here https://www.brainy-bits.com/make-any-arduino-pin-an-interrupt-pin/
///     Some of this code is based on Nicholas Chan's code for implementing a PID controller on a camera gimbal which can be found here: https://github.com/DavisDroneClub/gimbal 

// Sets code mode to run system diagnostics. This enables or disables logging information to the micro SD card. Additionally, serial monitoring can be toggled on and off here.
boolean diag = true; // toggles SD card logging
boolean serial = false; // toggles serial monitoring

/* 
* -------- Code Libraries --------
*/
#include <PID_v1.h>              // Library for PID features
#include <LiquidCrystal.h>       // Library for LCD display 
#include <SD.h>                  // Library for logging data to the SD card
#include <EEPROM.h>              // Library for using EEPROM
#include <SPI.h>                 // Library for SPI communications 
#include <PinChangeInterrupt.h>  // The following libraries enable hardware interrupts to be used on any pin of the nano
#include <PinChangeInterruptBoards.h>
#include <PinChangeInterruptPins.h>
#include <PinChangeInterruptSettings.h> 

/* 
* -------- Variable Declarations ---------
*/ 
// Hardware Pins
int genPin = A7;    // DC generator input pin
int Tpin = A6;      // Analog input pin for throttle trigger hall effect sensor input 
int plusPin = 17;    // Hardware interrupt pin INT0 for plus button
int minusPin = 19;   // Hardware interrupt pin INT1 for minus button
int outputPin = 3;  // Pin at which the output signal to the existing motor controller is sent
int csPin = 4;      // Chip select pin for SPI communication with the SD Card Module

// Variables Used For Button Debouncing
volatile unsigned long lastInterruptTimePlus = 0;
volatile unsigned long lastInterruptTimeMinus = 0; 

// Variables Used For Throttle Signal Averaging When Cruise Control is Off 
const int numReadings = 10;
int readings[numReadings];      // the readings from the analog input
int readIndex = 0;              // the index of the current reading
int total = 0;                  // the running total
int average = 0;

// LCD hardware pins 
int rs = 9; 
int en = 8;
int d4 = 7;
int d5 = 6;
int d6 = 5;
int d7 = 2;
LiquidCrystal lcd(rs, en, d4, d5, d6, d7); // Sets up the LCD display 

// Miscallaneous Variables
int Tsig; // Signal incoming from the throttle trigger hall effect sensor
unsigned long currTime; // Used for logging time in diagnostics 
File diagFile; // Creates a new file object  
int fileCounter; // Variable used for naming .txt file written to SD card  

// Variables used in loop timing for diagnostic purposes
int loopStartState; 
int ifState1; 
int ifState2;
int ifState3;
int ifState4; 
int cruiseControlState = 0; // Keeps track of whether or not cruise control is engaged or not. Default is disengaged.
double unfiltrdGenVoltage; // declared here as a global variable to log to SD card 
double filtrdGenVoltage; // declared here as a global variable to log to SD card 

// Variables for low pass filtering 
double pastFiltrdSpd = 0, d_pastFiltrdSpd = 0, pastSpd = 0, pastTime = 0; 
double cutoffFreq = .001; // cutoff frequency in Hz
struct filtrdVals {     // structure definition used to return two values from the low pass filter function call
  double filtrdRdng; 
  double d_filtrdRdng; 
  double unfiltrdRdng;
}; 

// Constants for converting DC generator voltage to speed in getSpeed() function
double
sf = 2*3.1415/60,     /* from dissertation */ \
m = 456.3862,         /* from dissertation */ \
b = -1.2846,          /* from dissertation */ \
rR = 0.341,           /* from modeling the human controlled bicycle [m] */ \
rD = 0.028985,        /* from dissertation [m] */ \
rC = 0.333375         /* from dissertation [m] */ \ 
;

// PID Library Setup 
double kp = 1.03, ki = 0.145, kd = 0.05; // Constants Acquired From Controller Design Stage
volatile double Setpoint = 0; // declared as volatile so that its value may be shared between the button Interrupt Service Routine Functions and the main program
double Input, Output;
PID motorPID(&Input, &Output, &Setpoint, kp, ki, kd, P_ON_M, DIRECT); // Creates PID object. See PID library documentation
int OutputWrite; // variable for writing output to motor controller as a PWM duty cycle 

/* 
* ------------ Setup Function ------------ 
*/ 
void setup() {
    
    if(serial) Serial.begin(9600); 
    
    // Initializing LCD 
    lcd.begin(16,2);
    lcd.clear();
    lcd.setCursor(0,0);
    lcd.print("Initializing...");
    delay(3000);
    lcd.clear();
    
    // Declaring Hardware Interrupts for plus and minus speed increment buttons
    attachPCINT (digitalPinToPCINT(plusPin), plusISR, RISING); 
    attachPCINT (digitalPinToPCINT(minusPin), minusISR, RISING);
    
    // Declaring pin modes for hardware I/O
    pinMode(genPin, INPUT);
    pinMode(Tpin, INPUT);
    pinMode(plusPin, INPUT);
    pinMode(minusPin, INPUT);
    pinMode(outputPin, OUTPUT);
    pinMode(A5, INPUT); 
    pinMode(csPin, OUTPUT);
    
    // Setting Button Pins to High 
    digitalWrite(plusPin, HIGH);
    digitalWrite(minusPin, HIGH);
    
    // PID library settings
    motorPID.SetOutputLimits(0,4.59);  // Cuts the PID output (V) at about the max output of the hall effect sensor at max throttle (measured at 940 bits ~4.59V) 
    motorPID.SetMode(AUTOMATIC); // turns PID on
    
    // Diagnostics
    if (diag) {
      
      // SD Card Initialization
      if (SD.begin()) {
        lcd.clear();
        lcd.setCursor(0,0);
        lcd.print("SD Card");
        lcd.setCursor(0,1);
        lcd.print("Rdy");
        delay(3000);
      }
      else {
        lcd.clear();
        lcd.setCursor(0,0);
        lcd.print("SD card");
        lcd.setCursor(0,1);
        lcd.print("init. failed"); 
        delay(2000);
        return;
      }  
       // Updating fileCounter variable 
      fileCounter = EEPROM.read(0); 
      fileCounter++;
      EEPROM.write(0,fileCounter);
    }
    
    // Printing ready message
    lcd.clear();
    lcd.setCursor(0,0);
    lcd.print("Ready");
    delay(3000); 
    lcd.clear(); 
    
   // Prepping for signal averaging of the throttle signal when cruise control is off 
   for (int thisReading = 0; thisReading < numReadings; thisReading++) {  // initializing readings array with zeros
    readings[thisReading] = 0;
   } 
   
   lcd.clear();

} // END SETUP FUNCTION


/* 
* ------------ Loop Function -------------- 
*/
void loop() { 
 
 // PASSING THROTTLE THROUGH THE NANO
 if(cruiseControlState == 0) {
   
   // Passing throttle signal through the Arduino 
   Tsig = analogRead(Tpin); 
   if (Tsig < 190) {                // If the throttle is at it's rest position there should be no output to the motor controller
     analogWrite(outputPin, 0); 
   }
   else {
    // Begin Averaging of the Throttle Signal
    total = total - readings[readIndex]; // subtract the last reading:
    // read from the sensor:
    readings[readIndex] = Tsig/4;
    // add the reading to the total:
    total = total + readings[readIndex];
    // advance to the next position in the array:
    readIndex = readIndex + 1;
  
    // if we're at the end of the array...
    if (readIndex >= numReadings) {
      // ...wrap around to the beginning:
      readIndex = 0;
    }
  
    // calculate the average:
    average = total / numReadings;
     
     analogWrite(outputPin, average);
   }
  
   if(serial) serialData(cruiseControlState, Setpoint, Tsig, average, Input, Output, currTime); // displays pertinent info to serial monitor 
   
   Input = getSpeed(); // Acquiring input here for logging purposes
   
   // Printing current speed on LCD
   lcd.setCursor(0,0);
   lcd.print("Current Spd");
   lcd.setCursor(0,1);
   lcd.print(Input);
   
   // Logging Data For Diagnostics
   if(diag) {
    ifState1 = 0; currTime = millis();
    logData(cruiseControlState, Setpoint, Tsig, Input, Output, currTime, fileCounter, loopStartState, ifState1, ifState2, ifState3, ifState4); 
    }
  }

 // CRUISE CONTROL INITIALIZATION
 if(digitalRead(plusPin) == LOW && digitalRead(minusPin) == LOW) {  // If the user has activated the cruise control 
    
   cruiseControlState = 1; Tsig = 0;  // Setting Tsig to zero here so that it does not trigger the condition for cruise control disengagement presented below     
   
   // Setting the current speed as the initial setpoint speed
   float currSpeed = getSpeed(); 
   currSpeed = 0.1*round(currSpeed*10.0); // rounds the current speed to the nearest 0.1m/s
   Setpoint = currSpeed; 
   
   // Setting up the display formating
   lcd.clear();
   
   // Top row for setpoint
   lcd.setCursor(0,0);
   lcd.print("SetPt:");
   lcd.setCursor(7,0);
   lcd.print(Setpoint);
   lcd.setCursor(12,0);
   lcd.print("m/s");
  
   // Bottom row for current speed
   lcd.setCursor(0,1);
   lcd.print("CurrSpd:");
   lcd.setCursor(9,1);
   lcd.print(Input);
   lcd.setCursor(13,1);
   lcd.print("m/s");
   
   Input = getSpeed(); // measures the new current speed as the input to the PID algorithim
   motorPID.Compute(); // computes the output 

   // THE HANDOFF // Cruise Control now takes over passing throttle signal to the motor controller
   analogWrite(outputPin, 0); // turns the output from the nano off
   OutputWrite = (int)Output * (255/5); // Converting Output [V] to PWM duty cycle
   analogWrite(outputPin, OutputWrite); // Writing output to motor controller 
 }

 // RUNNING THE PID ALGORITHM
 if(cruiseControlState == 1) {

    // Computing PID Output
    Input = getSpeed();
    motorPID.Compute();
    OutputWrite = (int)Output * (255/5); // Converting Output [V] to PWM duty cycle
    analogWrite(outputPin, OutputWrite); // Writing output to motor controller
    
    // Log performance data to serial monitor if diagnostics enabled
    if(serial) serialData(cruiseControlState, Setpoint, Tsig, average, Input, Output, currTime);
    
    //Updating the current speed on the LCD
    lcd.setCursor(9,1);
    lcd.print(Input); 

    //Updating the setpoint on the LCD 
    lcd.setCursor(7,0);
    lcd.print(Setpoint);
    
     // Logging Data For Diagnostics
    if(diag) {
     ifState3 = 0; currTime = millis();
     logData(cruiseControlState, Setpoint, Tsig, Input, Output, currTime, fileCounter, loopStartState, ifState1, ifState2, ifState3, ifState4); 
     }
    
   }

 // CHECKING FOR CONDITIONS FOR CRUISE CONTROL DISENGAGEMENT
 if(analogRead(Tpin) >= 700 && cruiseControlState == 1) {     // Threshoat 700 bits (~3.5V) 
   
   cruiseControlState = 0;
   Setpoint = 0; Output = 0; // Setting setpoint and output back to zero so they can be reinitialized next time cruise control is engaged
   
   // Letting the user know the cruise control is disengaging
   lcd.clear();
   lcd.setCursor(0,0);
   lcd.print("Cruise Control");
   lcd.setCursor(0,1);
   lcd.print("Disengaged");
   
   analogWrite(outputPin, 0); // turns off the output to  "flip the switch"
   delay(2000);
   lcd.clear(); 
   
   }  

} // END LOOP FUNCTION


/* 
* -------------- Utility Functions ----------- 
*/

// The following two functions are the Interrupt Service Routines (ISR) called when either the plus or minus buttons are pressed. 
// Each function contains an if statement that evaluates the amount of time that has passed since the last time the ISR was called, effectively debouncing the button
void plusISR() {
  if (millis() - lastInterruptTimePlus > 500) {
   Setpoint+=0.1;
   lastInterruptTimePlus = millis();
  }
}
void minusISR() {
  if (millis() - lastInterruptTimeMinus > 500) {
   Setpoint-=0.1;
   lastInterruptTimeMinus = millis();
  }
}

// function for 2nd order Butterworth low pass filter 
// This function is based on the one implemented here: 
// https://gitlab.com/mechmotum/row_filter/blob/master/row_filter/complementary.py
struct filtrdVals lowPassFilter(double cutoffFreq, double dt, double currentRdng, double pastRdng, double pastFiltrdRdng, double d_pastFiltrdRdng) {
  
  struct filtrdVals vals;
  
  // Comput coefficients of the state equation 
  double a = pow((2 * M_PI * cutoffFreq), 2);
  double b = pow(2,0.5) * 2 * M_PI * cutoffFreq;
  
  // Integrate the filter state equation using the midpoint Euler method with time step h 
  double h = dt; 
  double denom = 4 + 2*h*b + pow(h,2)*a;
  
  double A = (4 + 2*h*b - pow(h,2)*a)/denom;
  double B = 4*h/denom; 
  double C = -4*h*a/denom; 
  double D = (4 - 2*h*b - pow(h,2)*a)/denom; 
  double E = 2*pow(h,2)*a/denom; 
  double F = 4*h*a/denom; 
  
  vals.unfiltrdRdng = currentRdng;
  vals.filtrdRdng = A*pastFiltrdRdng + B*d_pastFiltrdRdng + E*(currentRdng + pastRdng)/2; 
  vals.d_filtrdRdng = C*pastFiltrdRdng + D*d_pastFiltrdRdng + F*(currentRdng + pastRdng)/2;
  
  return vals;
}

// function for converting generator voltage reading into velocity 
// See: http://moorepants.github.io/dissertation/davisbicycle.html#calibration 
double getSpeed() {
  
  unfiltrdGenVoltage = (double)analogRead(genPin); 
  
  // Filtering analogRead 
  double dt = millis() - pastTime; // pastTime is the time at which this function was last called
  struct filtrdVals vals = lowPassFilter(cutoffFreq, dt, unfiltrdGenVoltage, pastSpd, pastFiltrdSpd, d_pastFiltrdSpd);
  
  // Updating global variables with new "past" values 
  pastSpd = vals.unfiltrdRdng;              // This is the current unfiltered speed value
  pastFiltrdSpd = vals.filtrdRdng;          // This is the current filtered speed value
  d_pastFiltrdSpd = vals.d_filtrdRdng;      // This is the current derivative of the filtered speed value
  pastTime = millis();                      // This is the current time
  
  // Transforming genVoltage to a voltage value
  filtrdGenVoltage = vals.filtrdRdng;     // updating global variable for logging purposes
  double genVoltage = 2.0*vals.filtrdRdng; // multiply by 2 to account for the voltage divider
  genVoltage = genVoltage*(5.0/1023.0); // Converts digital output of analogRead to voltage
  
  // Converting voltage to speed
  double speed = (sf*(m*genVoltage+b)*rR*rD)/rC; // Calibration equation from http://moorepants.github.io/dissertation/davisbicycle.html#calibration 
  
  return speed; // Returns the filtered speed
} 


// function for logging performance information to an SD card for data logging. This function is totally customizable to display whatever is deemed necessary
void logData(int cruiseControlState, double Setpoint, int Tsig, double Input, double Output, unsigned long currTime, int fileCounter, int loopStartState, int ifState1, int ifState2, int ifState3, int ifState4) {
  String stringOne = String(fileCounter);
  String fileName = String("TEST_" + stringOne + ".txt"); 
  diagFile = SD.open(fileName, FILE_WRITE);
  if(diagFile) {  // Skips executing the function if the file did not open correctly
    
    diagFile.print(cruiseControlState);
    diagFile.print(",");
    diagFile.print(Setpoint);
    diagFile.print(",");
    //diagFile.print(Tsig * (5.0/1023.0));  // converts signal from throttle to a voltage
    diagFile.print(Tsig);  // Raw Tsig value from analogRead
    diagFile.print(",");
    diagFile.print(Input);
    diagFile.print(",");

    // Getting DC Generator Voltage
    diagFile.print(filtrdGenVoltage);
    diagFile.print(",");
  
    diagFile.print(Output);  // Raw output value before analogWrite
    diagFile.print(",");
    diagFile.print(currTime/1000.0);  
    
    // Printing Loop Timing Flags 
    diagFile.print(",");
    diagFile.print(loopStartState);
    diagFile.print(",");
    diagFile.print(ifState1);
    diagFile.print(",");
    diagFile.print(ifState2);
    diagFile.print(",");
    diagFile.print(ifState3); 
    diagFile.print(",");
    diagFile.print(ifState4);
    
    diagFile.print(",");
    diagFile.println(unfiltrdGenVoltage);
    
    diagFile.close();
    }
} 

// function for writing pertinent information to serial monitor for debugging. This function is totally customizable to display whatever is deemed necessary
void serialData(boolean cruiseControlState, double Setpoint, int Tsig, int average, double Input, double Output, unsigned long currTime) { 
  if (cruiseControlState == true) {
    Serial.print("|CC_on, ");
  } else {
    Serial.print("|CC_off, ");
  }
  Serial.print(Setpoint);
  Serial.print(",| ");
  //Serial.print(Tsig * (5.0/1023.0));  // converts signal from throttle to a voltage
  Serial.print(Tsig);  // Raw Tsig value from analogRead
  Serial.print(",");
  Serial.print(analogRead(A6));
  Serial.print(",");
  Serial.print(Tsig/4);
  Serial.print(","); 
  Serial.print((int)average);
  Serial.print(",");
  Serial.print(Input);
  Serial.print(",");

  // Getting DC Generator Voltage
  double genVoltage = 2.0*(double)analogRead(genPin);   // Multiply by two to account for voltage divider
  genVoltage = genVoltage*(5.0/1023.0); // Converts digital output of analogRead to voltage
  //Serial.print(genVoltage);
  //Serial.print(",");
  
  //Serial.print(Output * (5.0/255.0));  // Output in voltage
  Serial.print(Output);  // Raw output value before analogWrite
  Serial.print(","); 
  Serial.print((int)Output*(255/5));
  Serial.print(",");
  Serial.println(currTime/1000.0); 
}

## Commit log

2018-12-15 moved ButtonTester.ino and ThrottleTester.ino to local archive
2018-12-15 Remaking the TopLevel folder since the Arduino IDE insists that it be there
2019-02-10 Increasing threshold to 2V
2019-02-10 Adding DC gen voltage reading to serialData function
2019-06-24 Added measured time response data file, new controller tuning script to make sure motor is not pulling too much current
2019-07-15 Added some more clarifying comments and adjusted threshold values for throttle
2019-07-23 Fixed error with getSpeed() function by removing the use of map(), added OutputWrite variable to write output as a PWM duty cycle
    [TopLevel.ino]
2019-07-23 Added if statement to keep motor from spinning while throttle is at rest
2019-07-31 removed PID while loop and replaced it with if statements
    [TopLevel.ino]
2019-07-31 fixed errors in last commit
    [TopLevel.ino]
2019-08-01 Added changes to fix some issues during testing
    [TopLevel.ino]
2019-08-02 Added function for low pass filtering
2019-08-02 Updated filter cutoff freq
2019-08-05 Updated PID controller parameters
2019-08-08 added current speed reading to cc off mode
2019-08-18 updating code to current version
2019-10-08 removing old controller tuning code and replacing with updated code that includes power calculation
2019-10-14 Adding test files used in BMD materials
    These are the data files used in producing the figures in the BMD poster and paper
2019-11-18 Uploading cruise control system electrical schematic (pdf)
2019-11-18 Uploading Cruise Control System Electrical Schematic (easy EDA file)
2019-11-28 Deleting old version of electrical schematic to upload newer
2019-11-28 deleting old version of electrical schematic
2019-11-28 Adding updated electrical schematic (pdf)
2019-11-28 Uploading updated electrical schematic (easyEDA)
2019-12-18 Adding project's CAD files to the repo
    [AdjusterArm.STL, AdjusterArm.sldprt, Arduino Housing Master Assembly.SLDASM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]
